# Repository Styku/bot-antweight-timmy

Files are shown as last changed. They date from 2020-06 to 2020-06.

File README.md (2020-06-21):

# Timmy build guide

1. Get all of the components
2. Print the chassis
3. Solder electronics together
4. Program the transmitter

## Required components
Bear in mind that many of these parts may not be available or even produced anymore. Links are provided only for reference - just find something with similar characteristics and you'll be fine.
* 2x [Turnigy 15mm 75:1 motor](https://hobbyking.com/fr_fr/brushed-motor-15mm-6v-20000kv-w-75-1-ratio-gearbox.html)
* 2x [Brushed ESC](https://www.aliexpress.com/item/32888425852.html?spm=a2g0s.9042311.0.0.16024c4dQrNdOv)
* [Brushless motor](https://hobbyking.com/en_us/brushless-motor-d2205-2600kv-ccw.html)
* [Brushless ESC](https://hobbyking.com/en_us/afro-esc-12amp-multi-rotor-motor-speed-controller-simonk-firmware.html)
* [Saw blade](https://www.leroymerlin.fr/v3/p/produits/lame-bois-coupe-rapide-et-grossiere-dexter-power-pour-bois-e1400768268)
* [Turnigy NanoTech 2S LiPo](https://hobbyking.com/fr_fr/turnigy-nano-tech-370mah-2s-25-40c-lipo-pack.html)
* [Turnigy i6 receiver](https://hobbyking.com/fr_fr/turnigy-ia6-receiver-6ch-2-4g-afhds-2a-receiver.html)
* 3x 2.5 x 16mm wood screws

## Required tools
These will be absolutely necessary:
* Soldering iron
* Precision screwdriver (with Torx bits)
* Pliers or spanner for M3 nuts

And these are not, but will help:
* Hand file
* Hot glue gun
* Plumber's wrench
* Instant glue (any cyanoacrylate, eg. Superglue)

## Printing
You will find all of the required STLs in the stl folder. 
If you want to modify the design, feel free to fork the 
[OnShape project](https://cad.onshape.com/documents/876aae336eb09ce6dbed248a/w/df23d79c1c15b5b48407cba3/e/a6816d4151a04fb3a5ee5f1b).

### Chassis
All parts can be printed either with PLA, ABS or PETG. Original Timmy was
printed with PETG. __Chassis__ and its cover should be printed with layer height
<= 0.35 mm. For chassis, use supports.

### Wheels
For best traction, you will need to attach some additional rubber using instant
glue. In that case, you can print wheels using any filament available. In case
you do not want to glue any rubber, printing wheels in TPU will help with
traction. In that case, use the alternative design dedicated for TPU printing.

In any case, best print at layer height 0.2 mm.

### Saw blade mounting
No supports, 0.2 mm layer height. TPU would be the best material, but with a
drop of instant glue anything will do just fine.

## Electronics
There is nothing out of ordinary here, only generic stuff. I'll add a link to 
some RC model electronics tutorial

## Assembly
### Weapon
Weapon assembly here is a bit of improvisation, feel free to disregard whatever
you read here and do it your way if you feel like it.

1.  Screw an M3 nut onto the motor shaft. At this point you may want to fix the
    stator in place, for example by clamping it with plumber's wrench:

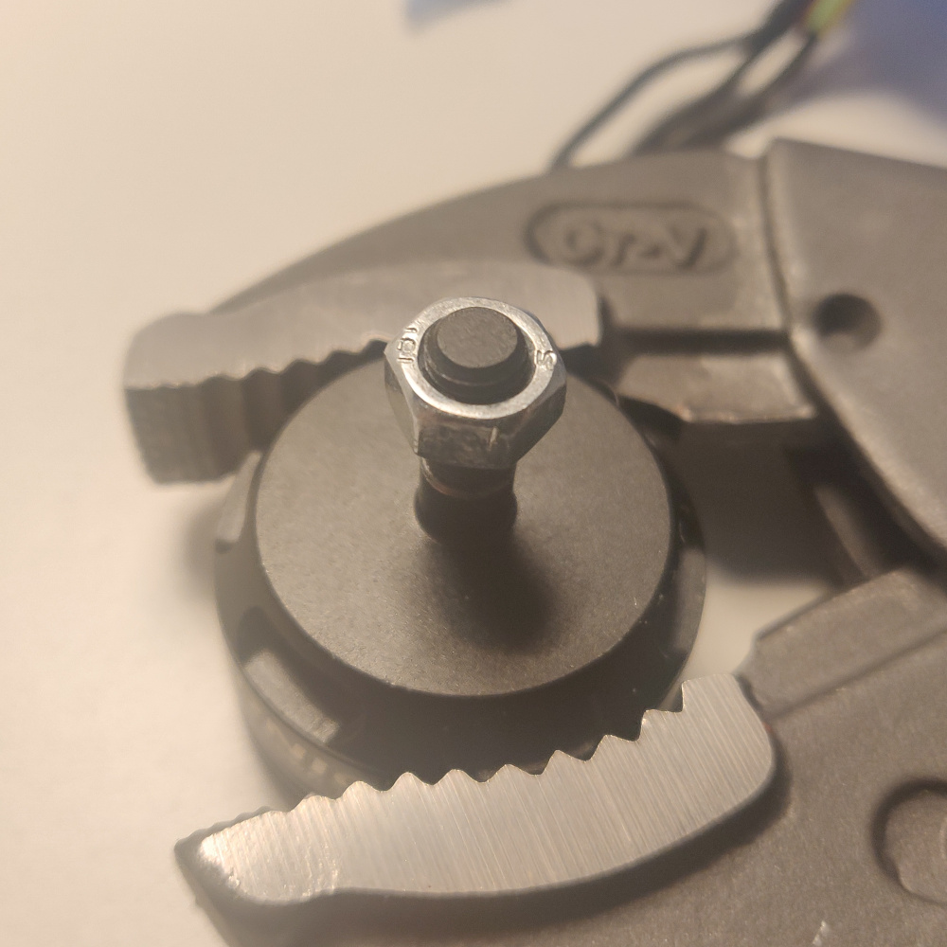
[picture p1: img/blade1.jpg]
Fix M3 nut
    

2.  Fix the printed part that has an M3 shaped slot in it. The nut you just
    fixed should fit right in there.

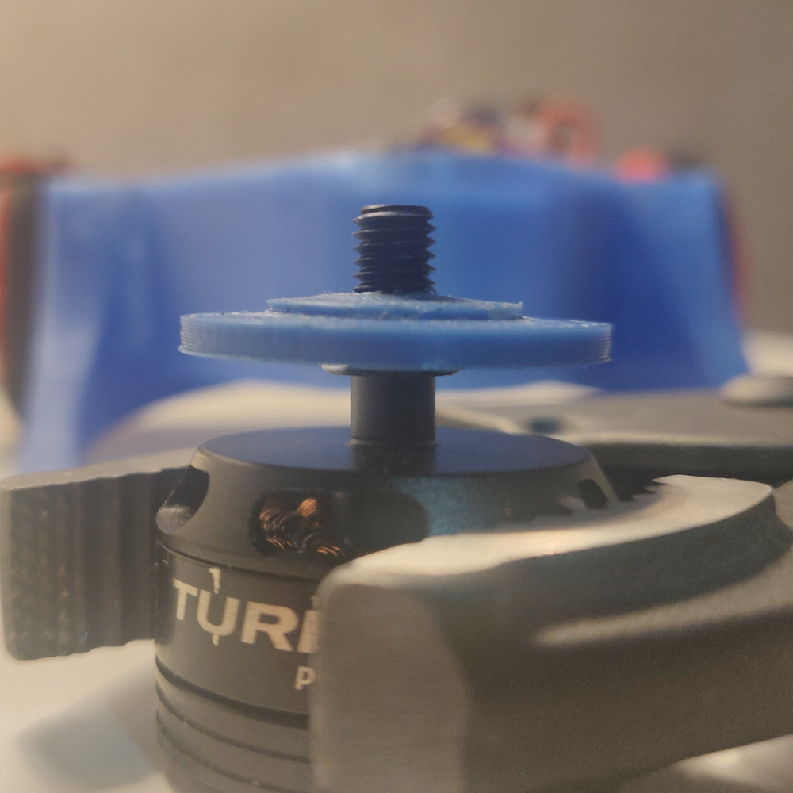
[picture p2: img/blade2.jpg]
Fix bottom part of the adapter
    

3.  Put the blade on. No need to care about the rotation direction too much,
    you'll be able to configure it with the transmitter.

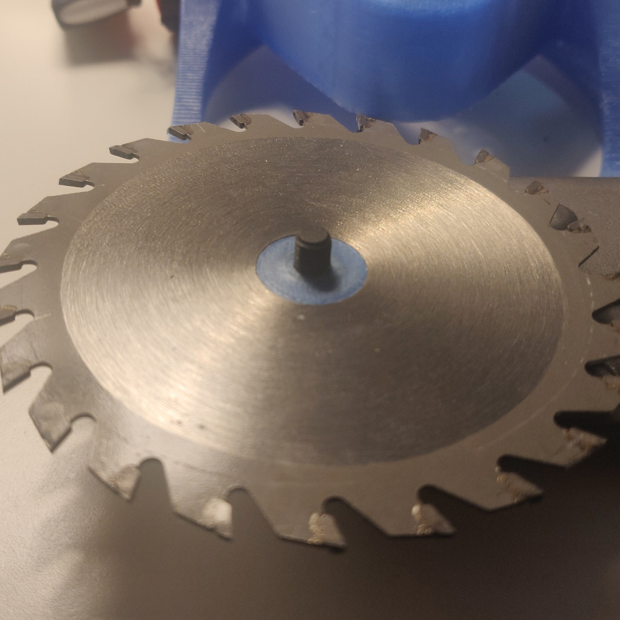
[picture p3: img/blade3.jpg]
Add the blade
    

4.  Now you have two options: 1) you can use instant glue to lock the blade
    in place between two 3D printed plastic parts, 2) you can add a layer of rubber
    hoping the friction will keep the blade spinning.

    Second option also acts as a safety clutch - it will prevent you from stalling
    and burning the motor, but at the same time make the weapon less effective.

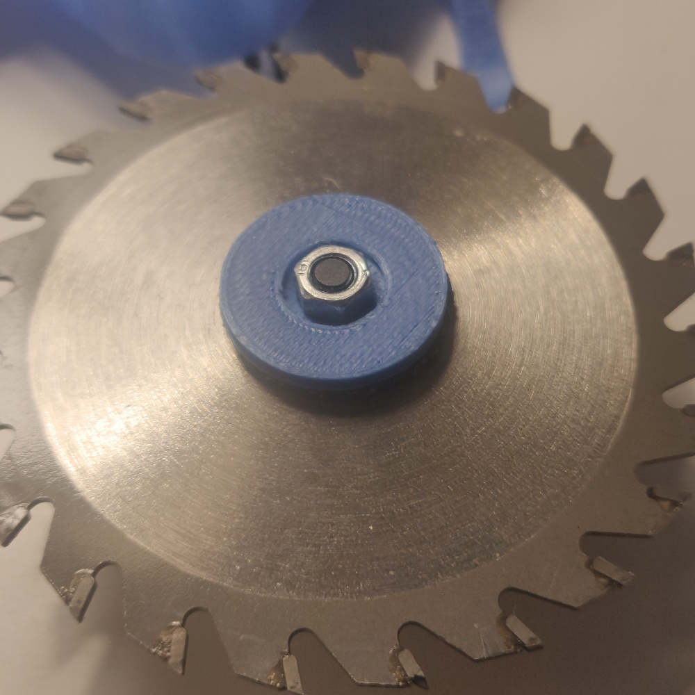
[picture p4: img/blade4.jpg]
Add the blade
    

### Chassis
Not much to be said here, just cram the soldered electronics inside. There are
two slots for motors (orientation again does not really matter), and a slot for
a master switch. As much as it is optional, I encourage you to include one, it
makes operating the robot much easier. I have made one out of the switch that
was included with the brushed ESC.

Guide the brushless ESC cables through the opening in the weapon motor slot like
this:

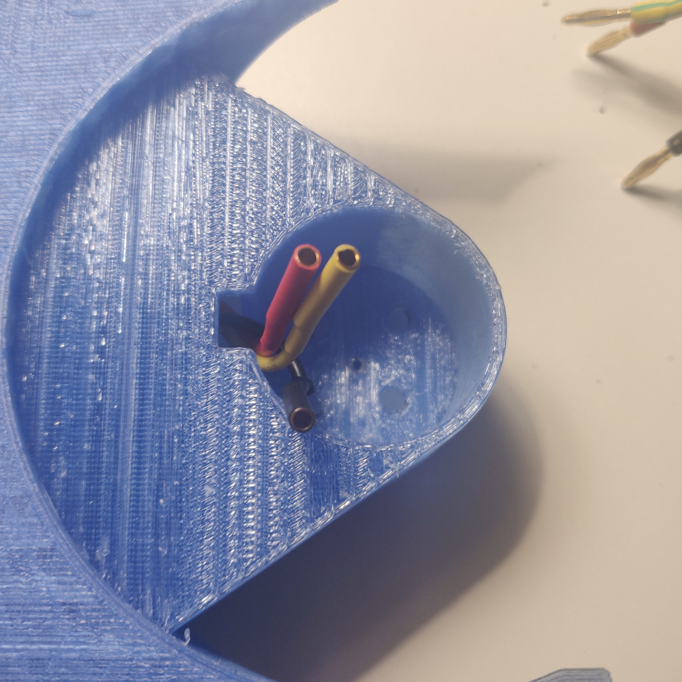
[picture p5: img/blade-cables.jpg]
Guide cables


Then, connect them to the motor. Put the motor in place and fix it with screws
that came with it.

When everything is in place, you may want to consider fixing it with
some hot glue (you should at least glue the master switch if you decided to
include it). Just be careful not to immobilize either the drive motor gearbox
or master switch moving part.

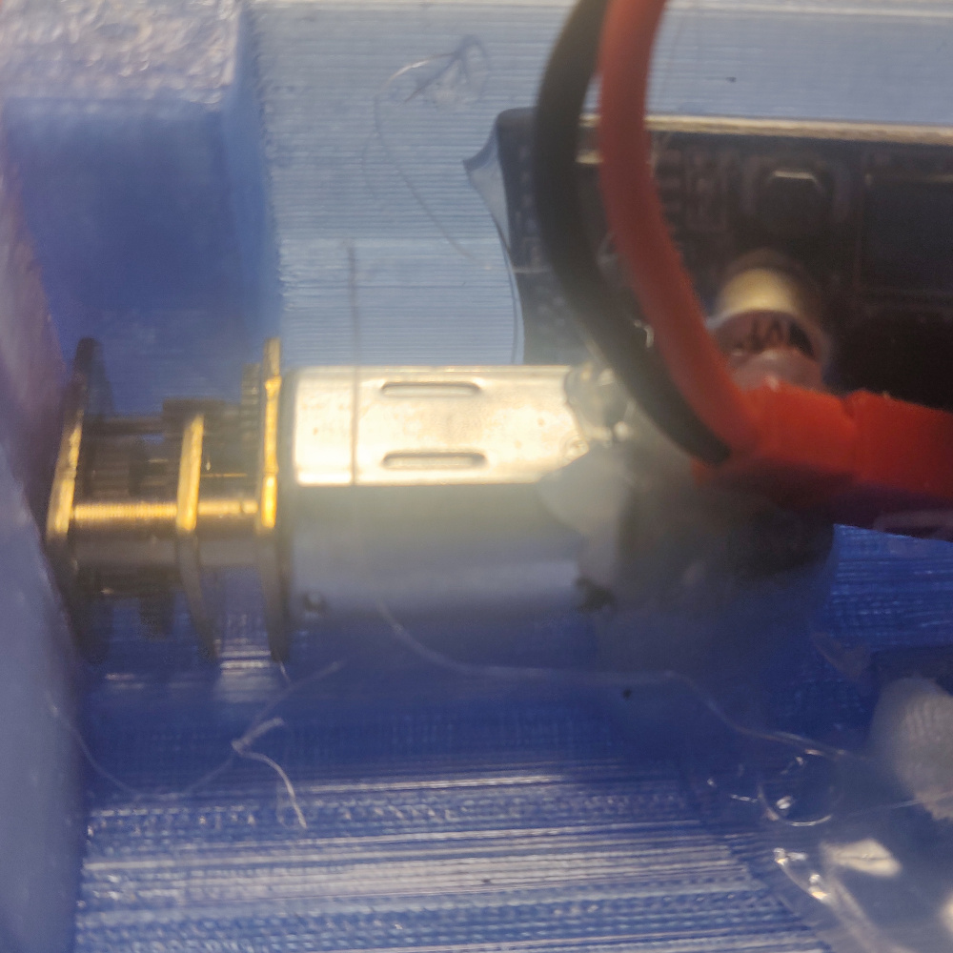
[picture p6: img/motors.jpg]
Glue the motor


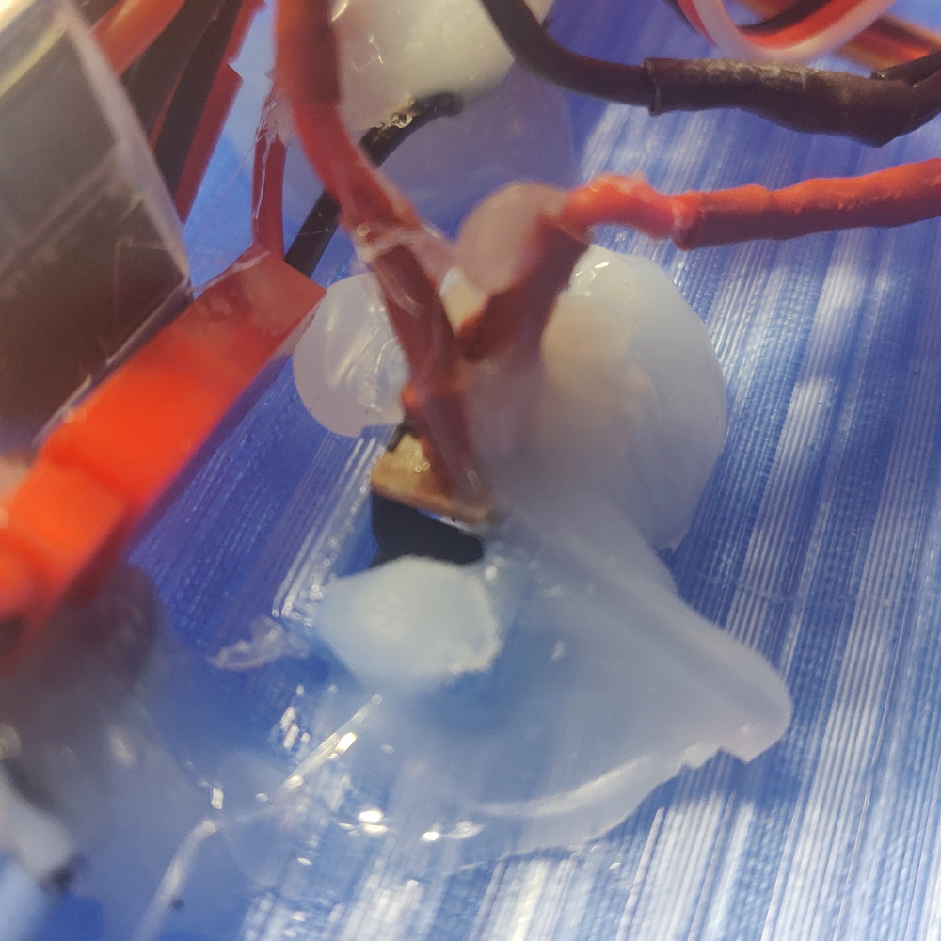
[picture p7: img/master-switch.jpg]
Glue the switch


Now cram down all the rest. Don't worry too much if some cables stick out, they
will be squeezed by the top cover.

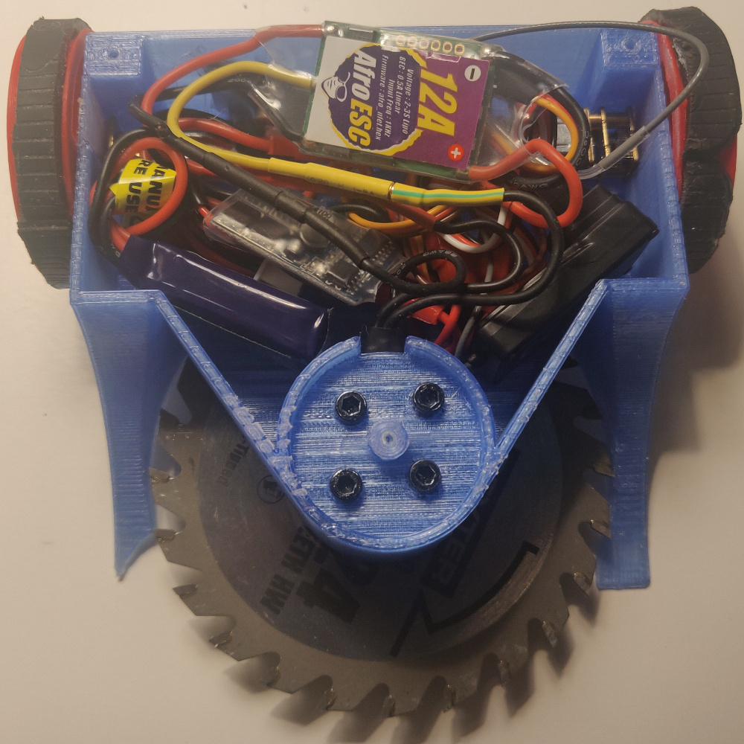
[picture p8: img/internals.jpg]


Put the top cover and screw it with 2.5mm wood screws. **Be careful with the one
over the weapon motor. Use a M3 nut to distance it from the cover so it does not
push against the motor.**

### Wheels
Glue some rubber around them. You can also use an old inner tube for a bike,
just cut it in about 8mm wide rings, stretch them and place and put them on.
They should hold nicely by themselves, no glue necessary.

If you printed them with layer height 0.2mm, they should snap right onto the
shafts with a bit of pressure and stay there. Drop of instant glue may be used
in addition if they are too loose. I personally have not glued them for the ease
of replacement. If the wheels do not fit, try filing the slot a bit.

## Finished build
There you go, what you have should resemble this guy:

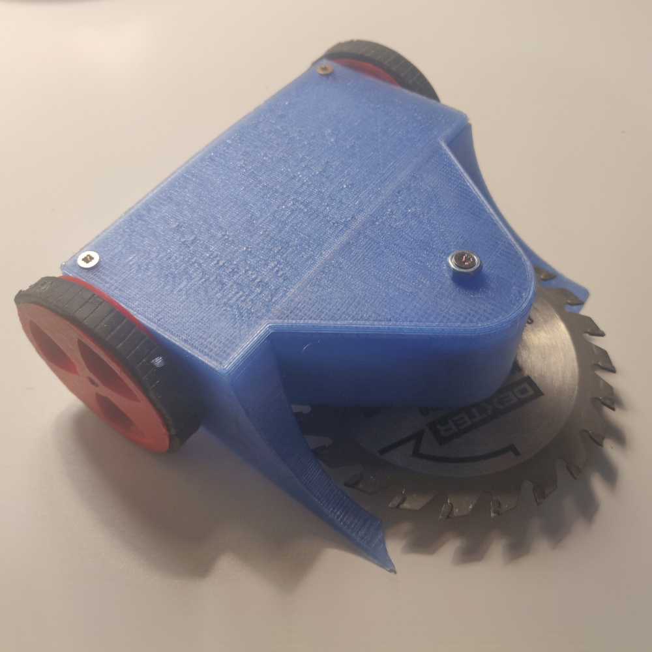
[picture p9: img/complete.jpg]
Finished bot


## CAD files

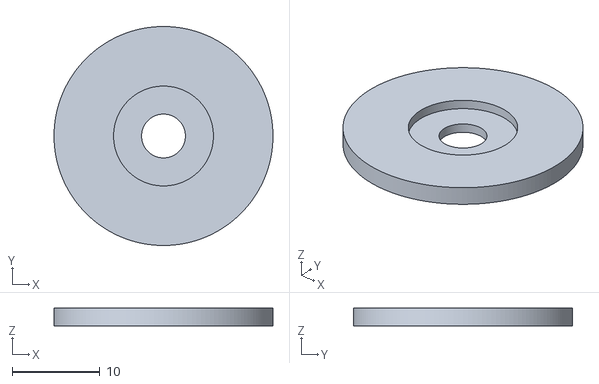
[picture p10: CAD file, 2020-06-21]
stl/blade-adapter-top.stl
25.0 x 25.0 x 2.00

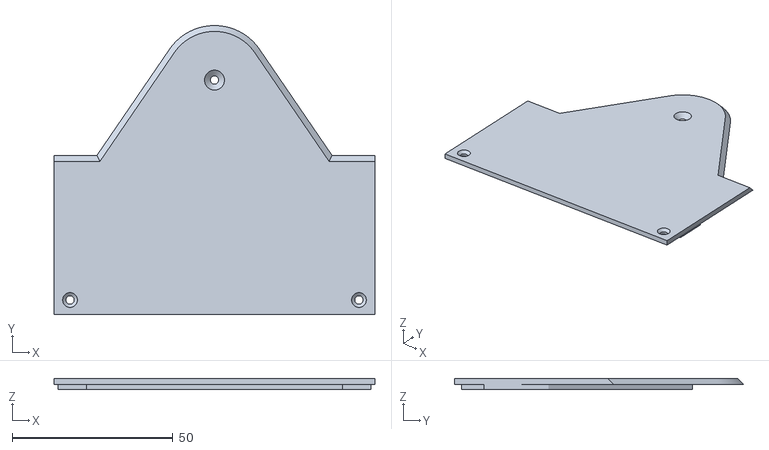
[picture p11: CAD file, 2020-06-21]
stl/chassis-cover.stl
100.0 x 90.0 x 3.43

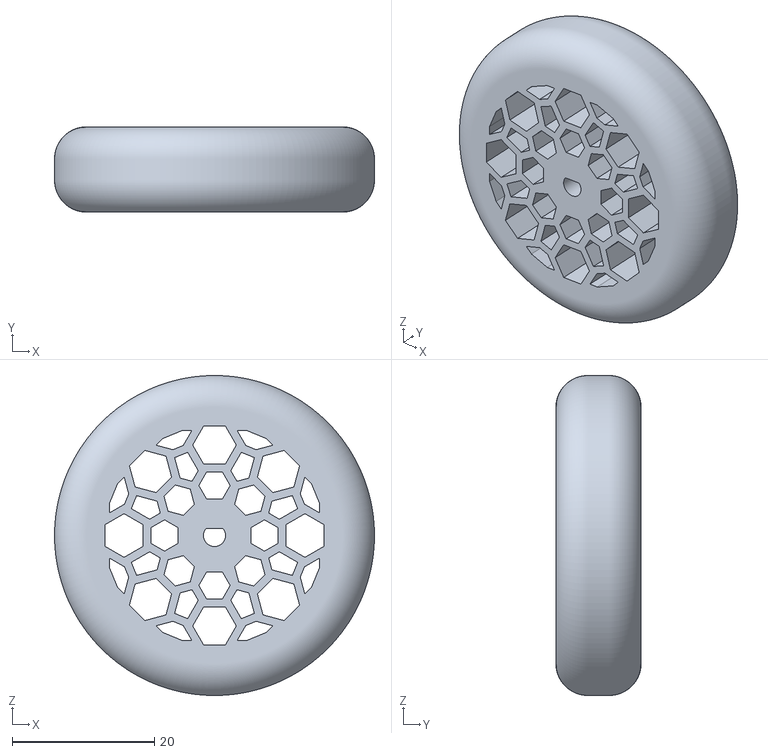
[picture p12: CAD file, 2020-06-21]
stl/wheel-tpu.stl
45.0 x 12.0 x 45.0

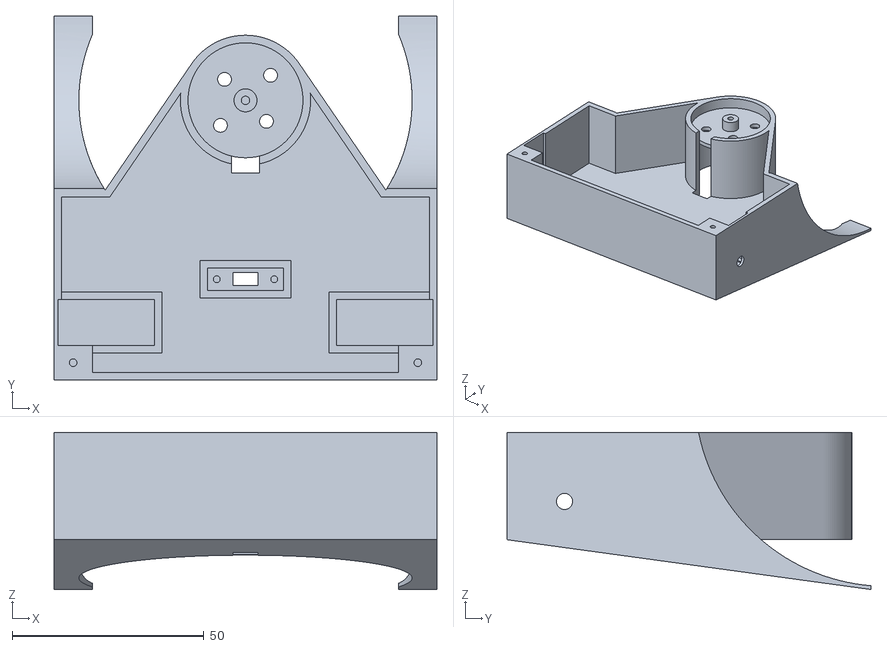
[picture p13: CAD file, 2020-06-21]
stl/chassis.stl
100.0 x 95.0 x 41.0

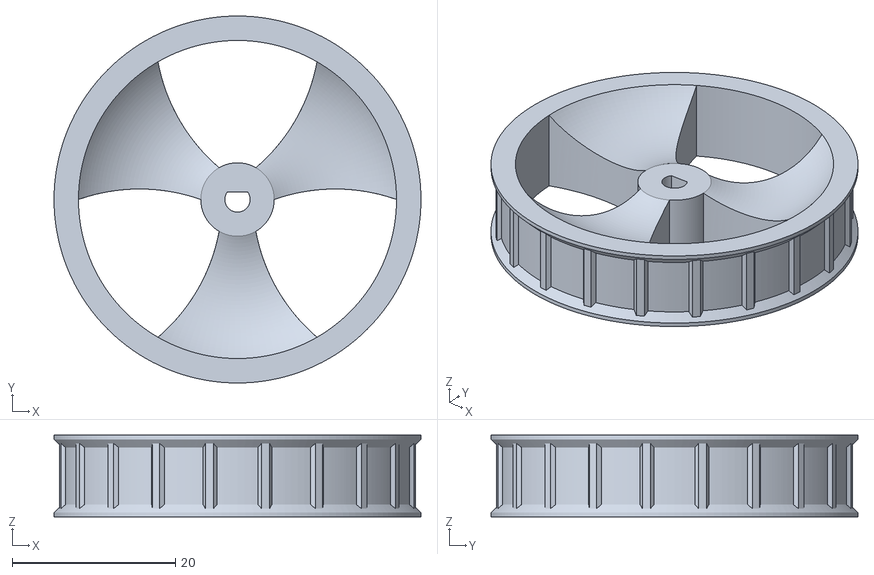
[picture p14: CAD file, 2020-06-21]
stl/wheel-petg.stl
45.0 x 45.0 x 10.0

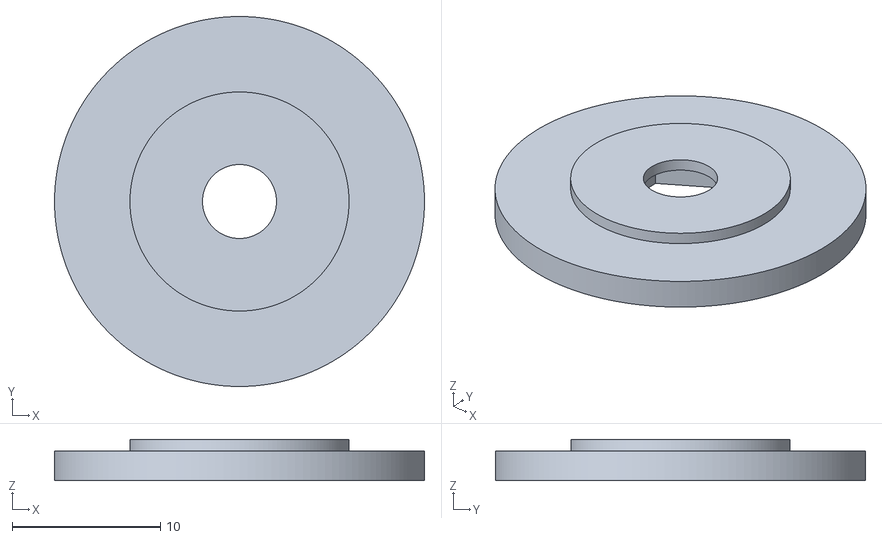
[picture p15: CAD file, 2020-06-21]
stl/blade-adapter-bottom.stl
25.0 x 25.0 x 2.80
